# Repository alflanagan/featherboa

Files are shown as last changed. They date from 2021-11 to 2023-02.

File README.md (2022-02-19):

# featherboa

Programmming a [FeatherS2 board](https://feathers2.io/) (ESP32-S2 chip) in Python. The actual implementation is the [CircuitPython port](https://circuitpython.org/board/unexpectedmaker_feathers2/) for the FeatherS2 board.

## What's with the name?

Feather is the name of the controller board I'm using for my robot, and a boa constrictor is, well, cousin to a python at least. (Hey, you try finding an original name on github).

## The Robot

The chip is being used to drive two Adafruit Feather [motor controllers](https://www.adafruit.com/product/2928). Each can drive 8 servos, but the robot uses 12, so they're divided into 6 servos/2 legs per board.

The robot body is based on a [Thingiverse Item](https://www.thingiverse.com/thing:50125)\*. I've included the OpenScad files in this repository, some of them have been re-written by me.

## Project Log

I am (trying to) maintain a [log](./docs/project_log.md) of the progress of this project. Hopefully if you're interested in this
project you can learn from my mistakes along the way.

---

\* Those files are covered by the Creative Commons license [CC BY-SA 3.0](https://creativecommons.org/licenses/by-sa/3.0/).

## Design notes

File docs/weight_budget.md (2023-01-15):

# Featherboa: Weight

## What is a Weight Budget?

For any mobile device, weight is an issue, for two main reasons. First, for a given set of wheels, tractors, or in our case legs, there's a maximum weight the chassis can support and still be able to move. Second, when moving, the more weight moved, the more energy it takes (see document [Energy Budget](energy_budget.md)). So the goal is to minimize the weight.

So a weight budget is the weight of all the pieces and parts, constrained by the amount the robot can reasonably carry.

Since our batteries are the second-largest source of extra weight, the weight budget puts limits on the energy budget, and vice-versa.

## Total Weight

                                |          | Weight|Per Unit |       |                                   |
Part                            | Quantity | Rated | Actual  | Total | Notes                             |
--------------------------------|----------|-------|---------|-------|-----------------------------------|
SG92R Servo Motor               |  12      | 9     | 11.65   | 139.8 | includes cable, mounting screws   |
1200 mAh LiPo battery           |  1       | 23    | 23      | 23    |                                   |
AA Battery, Duracell Alkaline   |  4       | 24    | 24.5    | 98    |                                   |
Leg mount (original)            |  2       |       | 2.5     | 5     |                                   |
Leg mount (wider)               |  2       |       | 4       | 8     |                                   |
Hip                             |  4       |       | 6.9     | 27.6  | includes horns, hot glue          |
4AA Battery Holder              |  1       |       | 11.3    | 11.3  |                                   |
Feather PCA9685 PWM controller  |  2       | 3.9   | 10.2    | 20.4  | Includes headers, 100uF capacitor |
FeatherS2 Microcontroller board |  1       |       | 6.2     | 6.2   | includes headers                  |
Upper Leg                       |  4       |       | 1.8     | 7.2   | includes motor horns, hot glue    |
Body (central bar)              |  1       |       | 0       | 0     |                                   |
Tibia (lower leg)               |  4       |       | 1.7     | 6.8   |                                   |

## Weight Limits

How much can the robot weigh? That's tricky. To stand, the robot needs to weigh less than the strength of the motors that hold the joints in a standing pose.

But we don't want our robot to just stand there, we want it to move. And that means at least one foot will be out of contact with the ground, so the remaining 3 legs have to be capable of bearing the weight.

One can get an estimate of the strength of the legs from the torque specifications of the motors, and the geometry of the parts (specifically the "ulna" and "tibia"). Or, one can directly measure the force required to cause the pose to break down and the leg to start moving.

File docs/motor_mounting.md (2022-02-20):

# Notes on Mounting SG92R MicroServo Motors

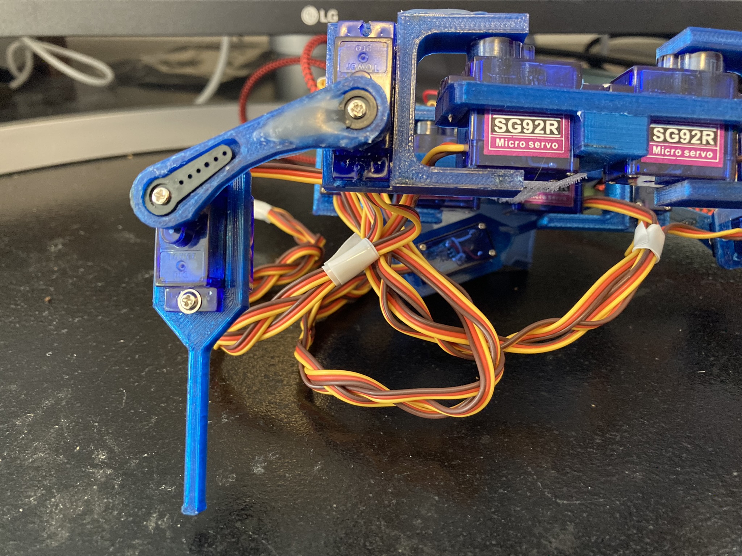
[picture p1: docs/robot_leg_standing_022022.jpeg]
robot leg with three motors


_One of four legs of the robot, more or less in a standing position. From the left, parts are a tibia, an ulna, and a hip. Farthest right is the hip of another leg._

## Overview

There are two basic points of connection between each motor and the body frame. The first is a rectangular hole that exactly fits the main body under the mounting lip. The second is the single point of contact with the gear which actually creates the motion.

This means there are four possible ways to mount each motor (although, as we'll see, some of them are equivalent for some parts.)

motor upright gear on left  motor upright gear on right

motor upside down gear on right
motor upside down gear on left

So the main motor can be on either side of the rectangular hole, and the gear is offset and can be on one side or other.

## The Joints

### Joint: Hip to Body

For the hip joint, the gear has to be on the outside or the joint won't fit. On the other hand, whether you mount the motor right side up or upside down doesn't matter (in terms of the hip motion), because the hip joint is symmetrical.

The only thing to keep in mind is that all the motors should be oriented one way or the other, to keep the sides balanced. Honestly, I'm not sure how much difference even that rule makes, as I haven't tried mixing them up.

### Joint: Hip to Ulna (Upper Leg)

In contrast, all four arrangments matter for this joint. The gear can be towards the top of the body, or towards the bottom; this affects the height (and possibly stability) of the robot. For now at least, I've chosen to mount them gear-down, for greater height. We'll see how it works.

Similarly, the gear can be pointing inside (towards the other leg), or outside away from the body. I've mounted the gears pointing toward the outside, to widen the stance, and reduce interference between front and rear legs on each side.

A further wrinkle: how you mount the motors will affect the code to drive the leg -- namely, does increasing the angle move the rest of the leg up, or down? Our code will have to reverse the rotation for some motors.

### Joint: Ulna to Tibia (Upper Leg to Lower)

The final joint is the lower leg, and the most important constraint is that the leg has to point down (duh). The tibia is symmetrical in the direction of the motor, so the only decision you have to make is whether the gear is on the upper side, or lower toward the "foot". I haven't found a good argument for mounting it lower. Other than that, how it attaches is already determined by how you've mounted the second motor.

## Range of Motion

Each motor has a range of motion, where the gear stops turning at a certain angle each way. You adjust the range of motion of the body part by mounting the horn on the gear at a certain angle.

I tried to set up each motor so that the range of motion of the gear matches the expected motion of the joint. Essentially I'd mount the horn on the gear and manually move the motor back and forth to the stopping points. To adjust the motion, I'd pop the horn off the gear and turn it one way or another, then press it down on the gear again. You may need tweezers or some sort of tool to help get the horn back off the gear.

## Attachment to Gear

The motors each come with two screws, and the body parts have corresponding mouting holes. There really isn't much to say about that other than the orientation as discussed above.

The attachment to the gear -- well, that's a different story. Notice that each gear attachment point has a hole for the gear, and a long shallow vaguely triangular depression in the body. The motors come with several "horns"\* which fit over the gear and extend to one side, or several, to allow connections with various parts. In particular, one horn fits over the gear and extends a triangular part in one direction -- which fits nicely into the depression in the body part.

So, all you have to do is fit the gear through the part with the depression facing up. Then we screw the horn on with the provided small screw, and the horn settles into the depression. When the gear turns, the horn efficiently transfers the force to the given part of the leg.

That's the theory. In reality, when I did that, I discovered a couple of problems. First, the part of the horn that fits over the gear is a bit longer than the hole in the part. Second, the depression is just a bit larger than the actual horn. I expect this is the inevitable result of getting your motors from different manufactures with slightly different specs.

The practical effect of that is that the connection between the motor gear and the leg part is loose, and the part is free to move both up and down the shaft, and back and forth rotationally. This makes for a very loose jointed robot, to the point that the leg becomes very unstable and the whole thing is in constant danger of falling apart.

One solution might be to redo all the parts with the thickness of the hole, and the size of the depression, adjusted to exactly fit the horns you have. I suspect that this will work, at least if the horn is of high enough quality. I haven't tried it as it means resizing a bunch of parts precisely, then re-printing them.

My first thought was: these parts are thermoplastic. If I warm the area to the point where the plastic is malleable, I might be able to reshape it to fit precisely to the horn. I don't know if you can actually do that. When I tried it, I discovered something important about the horns that came with my motors. Namely, the melting point of the plastic is lower than the melting point of the PLA thermoplastic used to print the body parts.

Scratch one body part, and one horm. Fortunately I ordered more motors than the 12 required for the robot, so I had extra. I highly recommend doing that, unless you're one of those people who gets things right on the first try. I have no idea what that would be like.

What I ended up using was a hot glue gun -- I stress again that this a prototype and doesn't have to be pretty. I was able (sometimes) to get the hot glue to fill the depression and stick to the body and the horn. I did not keep track of the number of times I had to retry it for some joints. If you've got a better solution, I'd _love_ to hear about it.

\* I have no idea why they're called that.

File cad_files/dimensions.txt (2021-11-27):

inner diameter center hole: 4.78mm
width of featherwing: 22.9mm
length of featherwing (w/o headers): 50.8mm
height of board + headers: 10.1mm
right-angle header width: 10mm

width lipo battery: 35mm
length lipo: 60mm
height lipo: 5.1mm

width of 4xAA holder: 30mm
height of holder: 32mm
length of holder: 58.6 mm

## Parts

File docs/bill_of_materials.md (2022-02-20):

| Quantity | Description | Supplier | Price EA | Total  |
| --- | --- | --- | --- | --- |
| ?? gms | Thermoplastic Resin for 3D Printer | | | |
| 2 | 8-Channel PWM or Servo FeatherWing Add-on For All Feather Boards | Adafruit | 9.95 | 19.90  |
| 1 | 3x4 Right Angle Male Header Adafruit (4-pack) | Adafruit | 2.95 | 2.95 |
| 1 | FeatherS2 - ESP32-S2 Feather Development Board | Adafruit | 24.95 | 24.95  |
| 1 | Adafruit Micro-Lipo Charger for LiPo/LiIon Batt w/MicroUSB Jack - v1 | Adafruit | 6.95 | 6.95 |
| 1 | Lithium Ion Polymer Battery - 3.7v 1200mAh | Adafruit | 9.95 | 9.95 |
| 12 | Micro servo Tower Pro SG92R | Adafruit | 5.95 | 71.40  |
| 1 | Battery holder: 4 x AAA | found item | | |
| 2 | 100uF 50V capacitor | found item | | |
| | Total Cost | | | 136.10 |

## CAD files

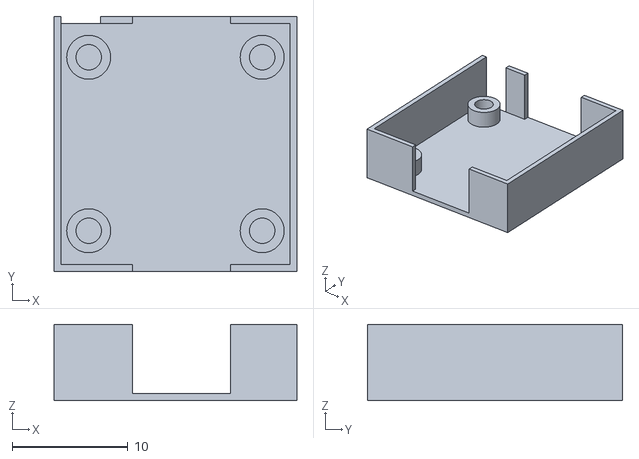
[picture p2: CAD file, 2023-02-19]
cad_files/power_boost.stl
21.0 x 22.1 x 6.60

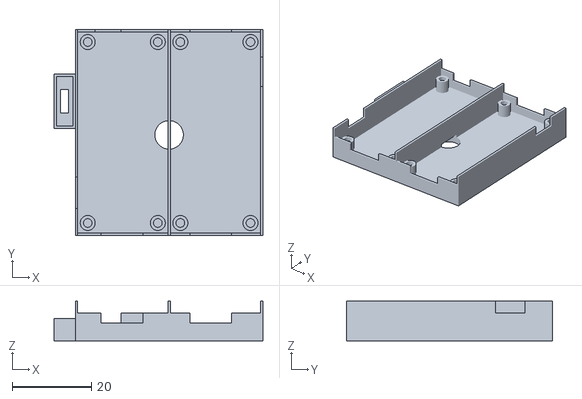
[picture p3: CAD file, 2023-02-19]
cad_files/board_tray2.stl
52.8 x 52.0 x 10.0

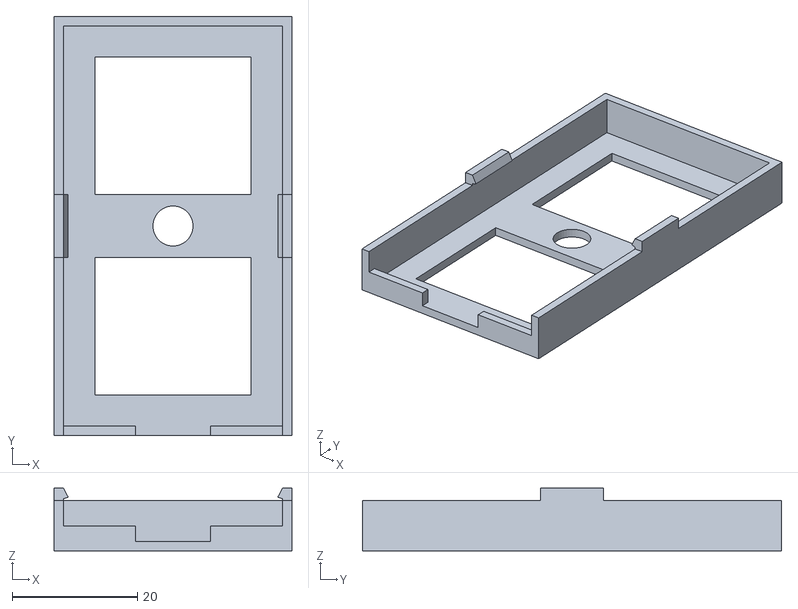
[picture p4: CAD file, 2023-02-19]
cad_files/battery_box.stl
38.0 x 67.0 x 10.0

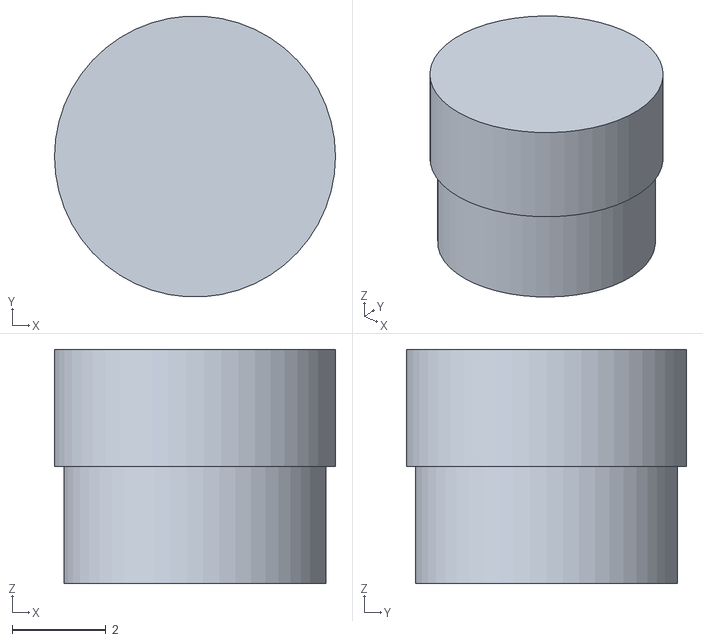
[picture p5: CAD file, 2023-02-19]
cad_files/center_post.stl
6.00 x 5.99 x 5.00

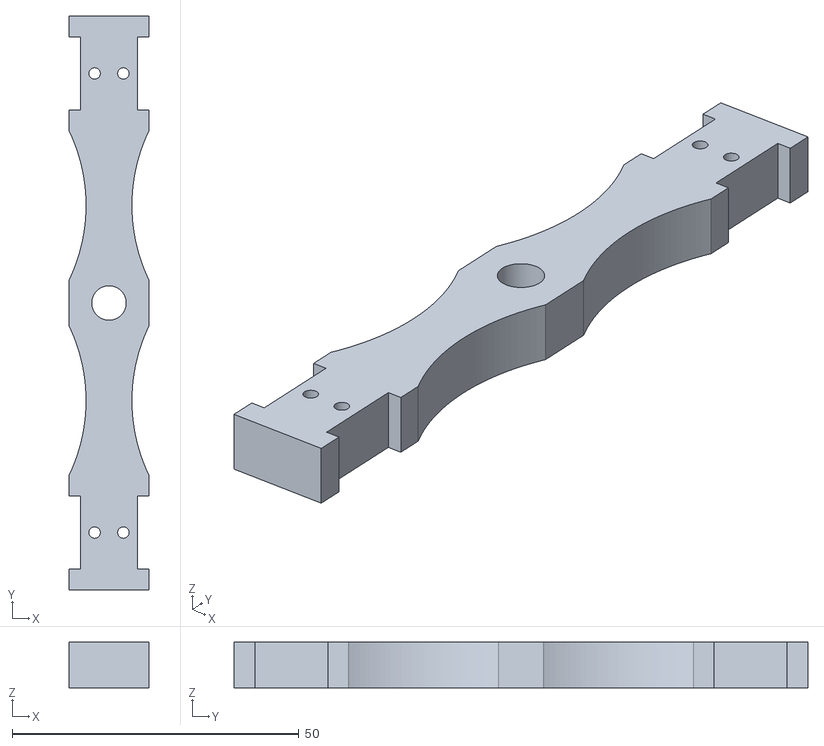
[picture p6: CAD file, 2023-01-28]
cad_files/backbone.stl
14.0 x 100.0 x 8.00

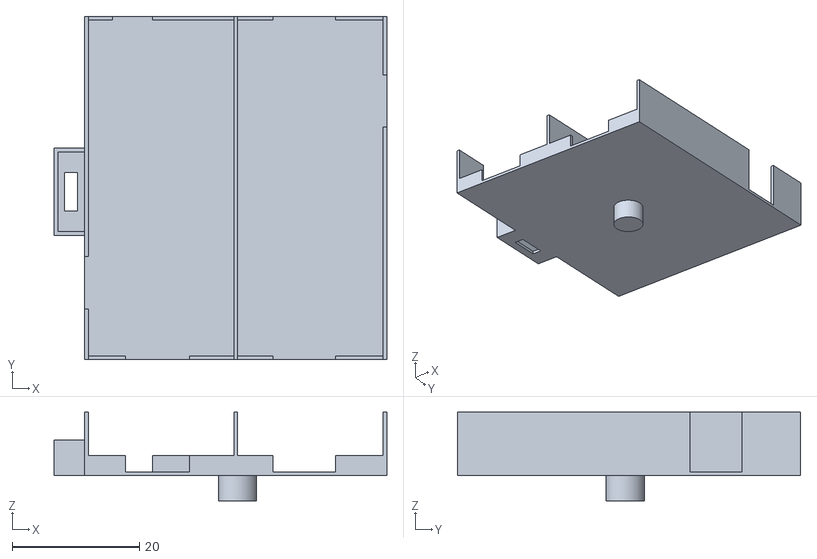
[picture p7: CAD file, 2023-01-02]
cad_files/board_tray.stl
52.4 x 54.0 x 14.0

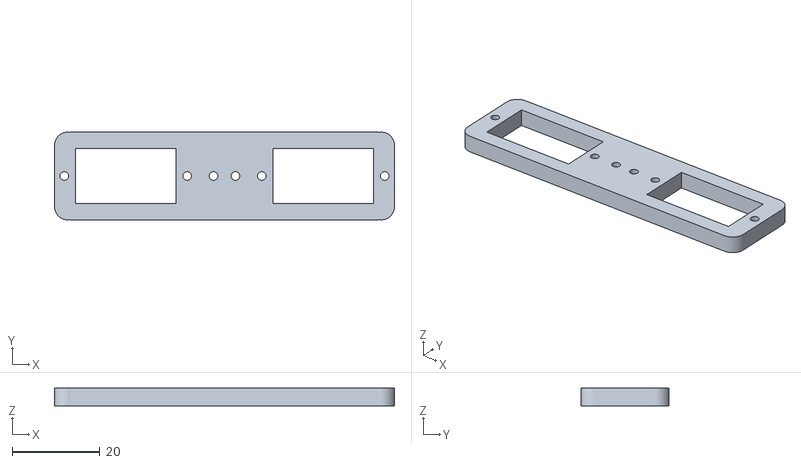
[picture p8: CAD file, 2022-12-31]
cad_files/hip2.stl
77.5 x 20.0 x 4.00

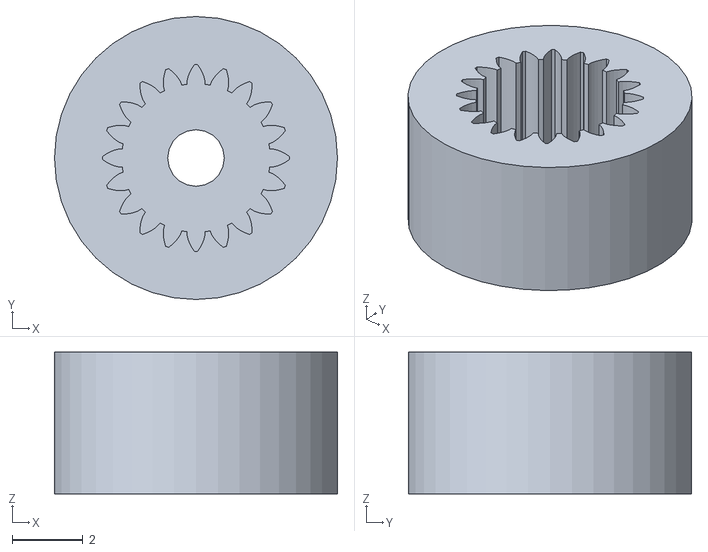
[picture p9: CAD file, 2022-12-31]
cad_files/sg92r_gear.stl
8.00 x 8.00 x 4.00

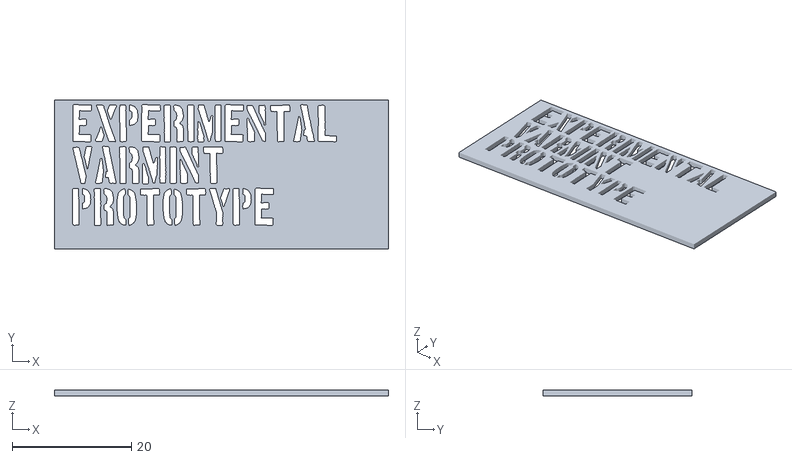
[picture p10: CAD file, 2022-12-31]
cad_files/signage.stl
56.0 x 25.0 x 1.00

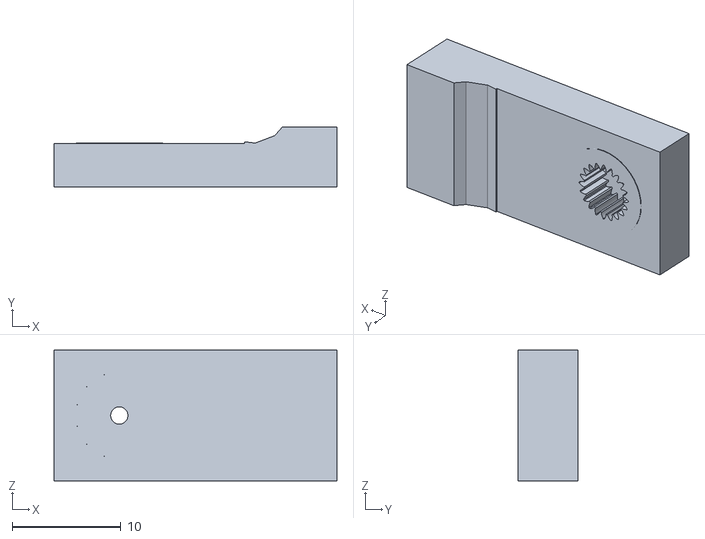
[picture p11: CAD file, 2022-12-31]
cad_files/coxa2.stl
26.0 x 5.50 x 12.0

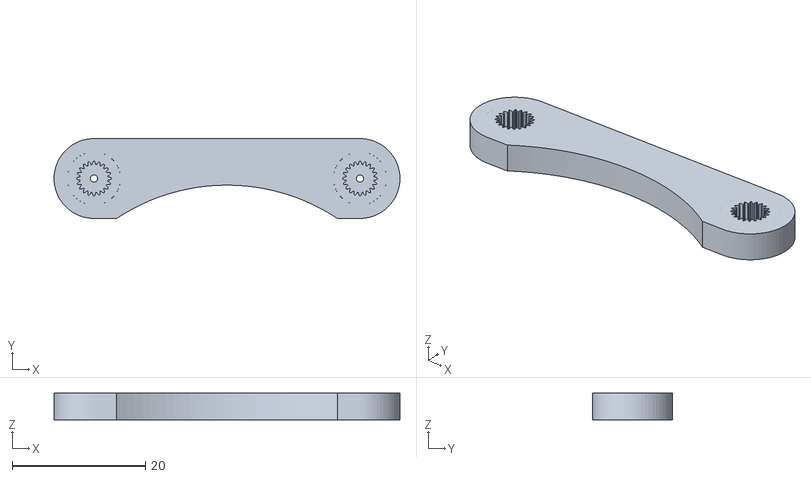
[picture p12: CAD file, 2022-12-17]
cad_files/femur.stl
52.0 x 12.0 x 4.00

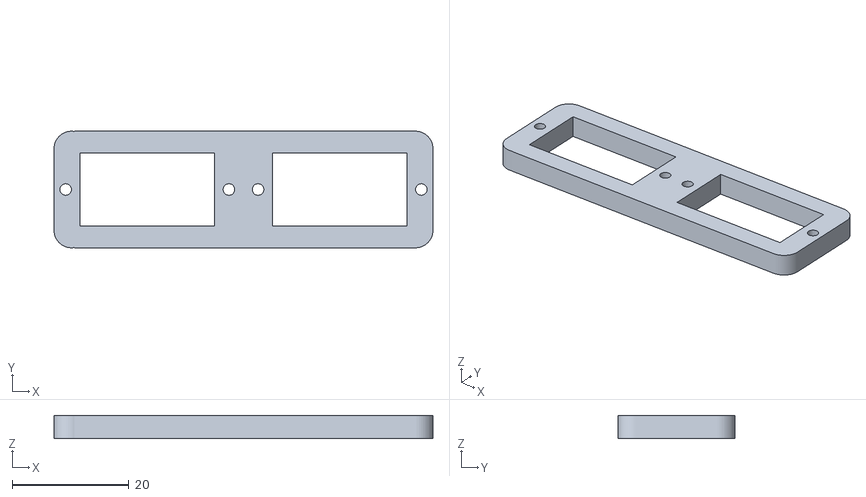
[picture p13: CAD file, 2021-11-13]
cad_files/hip.stl
65.0 x 20.0 x 4.00

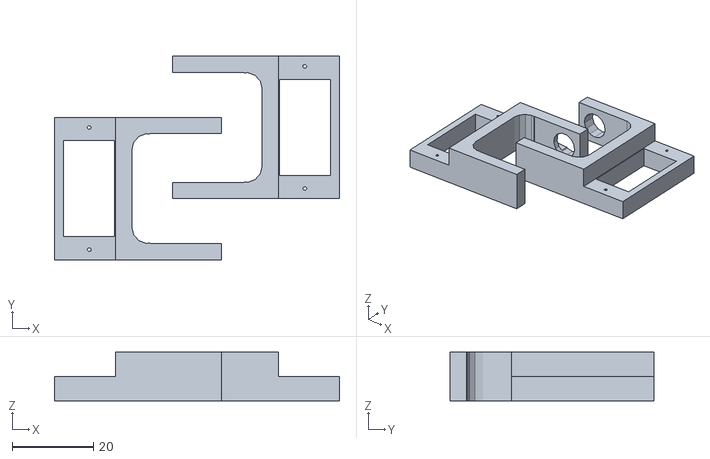
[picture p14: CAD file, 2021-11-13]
cad_files/coxa.stl
70.0 x 50.0 x 12.0

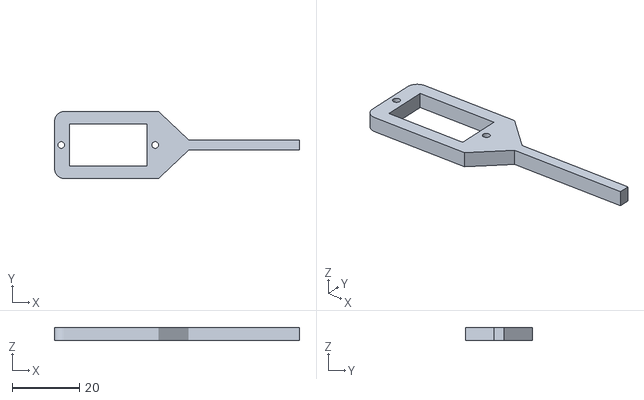
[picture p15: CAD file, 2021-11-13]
cad_files/tibia.stl
73.0 x 20.0 x 4.00

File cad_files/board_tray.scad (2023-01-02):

// tray for attaching feather boards to body assembly
// 1 unit = 1 mm

/* [Utility] */
// overlap to indicate joined objects
overlap = 0.01;

/* [Center Post] */
// center mounting hole in the backbone
center_hole_radius = 3;
// height of robot "backbone"
backbone_height = 8;

/* [Servo Board] */
// servo board w/power and right-angle headers
featherwing_width = 22.9;
// length of servo controller board
featherwing_length = 52.8;
// height of board + power post
featherwing_height = 10;

// mc board w/ through-hole leads
circuit_board_thickness = 2.6;

/* [Thickness] */
// sidewall width (also for end lips)
sidewall_width = 0.6;
// bottom thickness -- biggest effect on mass
tray_bottom_thickness = 0.6;
// thickness of switch box walls
switch_box_thickness = 0.6;

/* [Power Post Cutouts] */
// size of cutout for mc board power
power_post_width = 8.2;
// location of power cutout
power_post_from_end = 8;

/* [Power Switch Box] */
// width of power switch (y-dimension)
switch_width = 12.58;
// length of power switch (x-dimension)
switch_length = 4.19;
// height to hold switch but not block
switch_height = 5.6;
switch_wires_length = 2;
switch_wires_width = 6;

/* [End Lip Cutouts ] */
// usb-c connector on featherS2
usb_c_width = 10;
// distance from edge with power post cutout
usb_c_offset = 6.5;
// QWIIC (I2C) connector on featherS2
i2c_width = 6.3;
// distance from edge w/ power post cutout
i2c_offset = 4.42;
// motor controller headers
mc_width = 9.85;
// distance from edge w/ power post cutout
mc_offset = 7.5;

/* General Approach -----------------------------------------------------*/
/*
 * After a lot of experimentation, I've settled on the following best practice.
 * Each part is rendered by a module at 0, 0, 0 without translation (except
 * for overlap) or centering. <del>A separate module calculates the translation to
 * the final location.</del>
 * The final translation is done by the parent module / object.
 */

/* Parts  ---------------------------------------------------------------*/

/*
 * Draws a flat rectangle from 0,0,0, sized to hold two featherwing boards
 * parallel on the longer side. Includes space for sidewalls, etc.
 */
module
tray_bottom()
{
  cube([
    featherwing_width * 2 + sidewall_width * 3,
    featherwing_length + sidewall_width * 2,
    tray_bottom_thickness
  ]);
}

/*
 * Draws a vertical cylinder of a size to extend from the base through
 * the hole in the backbone part.
 */
module
center_post()
{
  cylinder($fn = 64,
           r = center_hole_radius,
           h = backbone_height / 2);
}

/*
 * Draws a flat rectangle the length of a feather board and height
 * of featherwing_height. Seperates and stabilizes the board position.
 */
module
sidewall()
{
  cube([
    sidewall_width + overlap,
    featherwing_length + 2 * sidewall_width,
    featherwing_height
  ]);
}


/*
 * Cutout in end_lip to allow access for USB-C connector or motor controller
 * headers (which are roughly the same width)
 */
module
usb_notch() {
  cube([
    usb_c_width, 
    sidewall_width + overlap * 2,
    featherwing_height
  ]);
}

/*
 * Cutout in end_lip to allow access for QWIIC connector.
 */
module
qwiic_notch() {
  cube([
    i2c_width, 
    sidewall_width + overlap * 2,
    featherwing_height
  ]);
}

/*
 * Cutout in sidewall to provide access to power supplies (battery connector for
 * micro, 5 volts for motor controllers).
 */
module
power_notch()
{
  translate([-overlap, -overlap, -overlap])
    cube([
      sidewall_width + overlap * 3, // 2 just not enough, somehow
      power_post_width,
      featherwing_height + overlap * 2
    ]);
}

/*
 * Cutout in end_lip to fit horizontal headers.
 */
module
mc_header_notch() {
  cube([
    mc_width, 
    sidewall_width + overlap * 2,
    featherwing_height
  ]);
}


/*
 * A low wall that spans the two board trays.
 */
module
end_lip()
{
  cube(
    [
      featherwing_width * 2 + sidewall_width * 3,
      sidewall_width,
      tray_bottom_thickness + circuit_board_thickness
    ]
  );
}

/*
 * A small box to contain a switch I happened to have on hand.
 * You'll need to at least set switch_length and switch_width to match
 * your switch, and possibly modify the cutout for the leads.
 */
module
switch_holder()
{
  difference()
  {
    union()
    {
      cube([ switch_length, switch_width, switch_box_thickness ]);
      translate([ 0, -switch_box_thickness + overlap, 0 ])
        cube([ switch_length, switch_box_thickness, switch_height ]);
      translate([ 0, switch_width - overlap, 0 ])
        cube([ switch_length, switch_box_thickness, switch_height ]);
      translate([ -switch_box_thickness + overlap, -switch_box_thickness, 0 ])
        cube([
               switch_box_thickness,
               switch_width + switch_box_thickness * 2,
               switch_height
        ]);
      translate([ switch_length - overlap, -switch_box_thickness, 0 ])
        cube([
          switch_box_thickness,
          switch_width + switch_box_thickness * 2,
          switch_height
        ]);
    } // union
    translate([
      (switch_length - switch_wires_length) / 2,
      (switch_width - switch_wires_width) / 2,
      -switch_box_thickness / 2
    ])
      cube([
        switch_wires_length,
        switch_wires_width,
        switch_box_thickness * 2
      ]);
  }; // difference
}



/* Assembly ---------------------------------------------------------------*/

module
board_tray()
{
  difference()
  {
    union()
    {
      tray_bottom();
      sidewall();
      translate([featherwing_width + sidewall_width, 0, 0])
        sidewall();
      translate([(featherwing_width + sidewall_width) * 2, 0, 0])
        sidewall();
      end_lip();
      translate([0, featherwing_length + sidewall_width, 0])
        end_lip();
      translate([-switch_length, (featherwing_length - switch_width) / 2, 0])
        switch_holder();
      translate([
        featherwing_width + 2 * sidewall_width,
        featherwing_length / 2,
        -backbone_height / 2 + overlap
      ])
        center_post();
    }  // union
    translate([0, power_post_from_end, tray_bottom_thickness])
      power_notch();
    translate([
      featherwing_width * 2 + sidewall_width * 2,
      featherwing_length - power_post_width - power_post_from_end,
      tray_bottom_thickness
    ])
      power_notch();
    translate([usb_c_offset, -overlap, tray_bottom_thickness])
      usb_notch();
    translate([
      i2c_offset, 
      featherwing_length + sidewall_width - overlap,
      tray_bottom_thickness
    ])
      qwiic_notch();
    translate([
      (featherwing_width + sidewall_width) * 2 - mc_width - mc_offset,
      -overlap,
      tray_bottom_thickness
    ])
      mc_header_notch();
    translate([
      (featherwing_width + sidewall_width) * 2 - mc_width - mc_offset,
      featherwing_length + sidewall_width - overlap,
      tray_bottom_thickness
    ])
      mc_header_notch();
  } // difference
}

board_tray();

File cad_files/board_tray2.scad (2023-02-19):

include <screw_holders.scad>;

// tray for attaching feather boards to body assembly
// 1 unit = 1 mm

/* [Utility] */
// overlap to indicate joined objects
overlap = 0.01;

/* [Center Post] */
// center mounting hole in the backbone
// upper part is a bit wider -- see center_post.scad
// center_hole_radius = 3.15; // 2.84 in real life, 4 => 3.76
center_hole_radius = 3.7;
// height of robot "backbone"
backbone_height = 8;

/* [Servo Board] */
//https://learn.adafruit.com/adafruit-feather/feather-specification?view=all#feather-and-wing-sizes-2861831
// servo board w/power and right-angle headers
featherwing_width = 22.8;
// length of servo controller board
featherwing_length = 50.8;
// height of board + power post
featherwing_height = 10;
hole_to_hole_narrow = 17.7;
hole_to_hole_wide = 45.7;

// mc board (includes screw holes)
circuit_board_thickness = 5;

/* [Thickness] */
// sidewall width
sidewall_width = 0.6;
// bottom thickness -- biggest effect on mass
tray_bottom_thickness = 2;
// tray_bottom_thickness = 0.8;

// z-offset of center post and matching hole
center_post_offset = -backbone_height / 2 - tray_bottom_thickness - overlap;

/* [Power Switch Box] */
// width of power switch
switch_width = 12.58;
// length of power switch
switch_length = 4.19;
// height to hold switch but not block
switch_height = 5.6;
switch_wires_length = 2;
switch_wires_width = 6;
// thickness of switch box walls
switch_box_thickness = 0.6;

/* [Board i2c Connector] */
// distance from edge
board_i2c_to_edge = 5;
// width of connector
board_i2c_width = 6.55;

/* [Board Power Connector] */
board_pwr_width = 8.0;
board_pwr_to_edge = 6.8;

/* [USB Connector] */
// actual connector not this wide, but board tab is
// distance from edge to start of tab
usb_to_edge = 6.5;
// width of tab
usb_width = 10.65;

/* [Motor Controller] */
// size of cutout for mc board power
power_post_width = 7.5;
// location of power cutout
power_post_from_end = 5.7;
// motor connections
side_header_width = 10.5;
side_header_offset = 6.1;


/* General Approach -----------------------------------------------------*/
/*
 * After a lot of experimentation, I've settled on the following best practice.
 * Each part is rendered by a module at 0, 0, 0 without translation (except
 * for overlap) or centering. A separate module calculates the translation to 
 * the final location.
 */
 
/* Parts  ---------------------------------------------------------------*/

/*
 * Draws a flat rectangle from 0,0,0, sized to hold two featherwing boards
 * parallel on the longer side. Includes space for sidewalls, etc.
 */
module
tray_bottom()
{
    cube(
        [
            featherwing_width * 2 + sidewall_width * 3,
            featherwing_length + sidewall_width * 2,
            tray_bottom_thickness
        ]
    );
}

/*
 * Draws a vertical cylinder of a size to extend from the base through
 * the hole in the backbone part.
 */
module
center_post()
{
    cylinder($fn = 50,
             r = center_hole_radius,
             h = tray_bottom_thickness + backbone_height / 2);
}


/*
 * Draws a flat rectangle the length of a feather board and height
 * of featherwing_height. Seperates and stabilizes the board position.
 */
module
sidewall()
{
    cube([ 
        sidewall_width + overlap, 
        featherwing_length + 2 * sidewall_width,
        featherwing_height 
    ]);
}

module
power_notch()
{
    cube([
            sidewall_width + 1,
            power_post_width,
            featherwing_height
        ]);
}

module
end_lip(xmul)
{
        cube([
                xmul * (featherwing_width * 2 + sidewall_width * 3),
                sidewall_width,
                tray_bottom_thickness +
                circuit_board_thickness
            ]);
}

module
switch_holder()
{
    difference()
    {
        union()
        {
            cube([ switch_length, switch_width, switch_box_thickness ]);
            translate([ 0, -switch_box_thickness + overlap, 0 ])
                cube([ switch_length, switch_box_thickness, switch_height ]);
            translate([ 0, switch_width - overlap, 0 ])
                cube([ switch_length, switch_box_thickness, switch_height ]);
            translate(
                [ -switch_box_thickness + overlap, -switch_box_thickness, 0 ])
                cube([
                    switch_box_thickness,
                    switch_width + switch_box_thickness * 2,
                    switch_height
                ]);
            translate([ switch_length - overlap, -switch_box_thickness, 0 ])
                cube([
                    switch_box_thickness,
                    switch_width + switch_box_thickness * 2,
                    switch_height
                ]);
        }
        translate([
            (switch_length - switch_wires_length) / 2,
            (switch_width - switch_wires_width) / 2,
            -switch_box_thickness / 2
        ])
            cube([
                switch_wires_length,
                switch_wires_width,
                switch_box_thickness * 2
            ]);
    };
}

module
board_i2c()
{
    cube([board_i2c_width, sidewall_width + 2 * overlap, featherwing_height]);
}

module
usb_connector()
{
    cube([usb_width, sidewall_width + 2 * overlap, featherwing_height]);
}

module
motor_connections()
{
    cube([side_header_width, sidewall_width + 2 * overlap, featherwing_height]);
}

module
board_power()
{
    cube([sidewall_width + 1,
          board_pwr_width,
          featherwing_height]);
}

/* Assembly ---------------------------------------------------------------*/

module
board_tray()
{
    difference()
    {
        union()
        {
            tray_bottom();
            sidewall();
            translate([featherwing_width + sidewall_width, 0, 0])
                sidewall();
            translate([(featherwing_width + sidewall_width) * 2, 0, 0])
                sidewall();
            end_lip(1);
            translate([0, featherwing_length + sidewall_width, 0])
                end_lip(1);
            translate([-switch_length - sidewall_width + overlap, 
                       featherwing_length * 2 / 3 - switch_width / 2,
                       0])
                switch_holder();
            translate([featherwing_width + sidewall_width, sidewall_width, 0])
              rotate([0, 0, 90])
                four_holes(tray_bottom_thickness);
            translate([(featherwing_width + sidewall_width) * 2,
                        sidewall_width,
                        0])
              rotate([0, 0, 90])
                four_holes(tray_bottom_thickness);
        }
                translate([(featherwing_width * 2 + sidewall_width * 3) / 2,
                            featherwing_length / 2,
                            center_post_offset / 2])
                    center_post();
        translate([board_i2c_to_edge, 
                   featherwing_length + sidewall_width - overlap,
                   tray_bottom_thickness + circuit_board_thickness / 2])
            board_i2c();
        translate([usb_to_edge,
                   -overlap,
                   tray_bottom_thickness + circuit_board_thickness / 2])
            usb_connector();
        translate([featherwing_width * 2 - side_header_width - side_header_offset,
                   featherwing_length + sidewall_width - overlap,
                   tray_bottom_thickness + circuit_board_thickness / 2])
            motor_connections();
        translate([featherwing_width * 2 - side_header_width - side_header_offset, 
                   -overlap, 
                   tray_bottom_thickness + circuit_board_thickness / 2])
            motor_connections();
        translate([-overlap, board_pwr_to_edge, tray_bottom_thickness + circuit_board_thickness])
            board_power();
        translate([featherwing_width * 2 + sidewall_width * 2 - 0.5,
                   featherwing_length - power_post_width - power_post_from_end,
                   tray_bottom_thickness + circuit_board_thickness])
            power_notch();
    }
}

board_tray();

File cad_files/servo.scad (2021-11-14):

// 3dof quad
//
// servo

module
servo(a = 30,
      b = 23,
      c = 27,
      d = 12,
      e = 33,
      f = 16,
      flange_thickness = 2,
      top_cap_pct = 0.5)
{
    rem_height = c - flange_thickness - f;
    top_cap_height = rem_height * top_cap_pct;
    roundel_height = rem_height * (1.0 - top_cap_pct);

    translate([ 0, -d / 2, 0 ]) union()
    {
        translate([ 0, 0, flange_thickness / 2 ])
            cube([ d, e, flange_thickness ], center = true);
        translate([ 0, 0, -f / 2 ]) cube([ d, b, f ], center = true);
        translate([ 0, 0, flange_thickness + top_cap_height / 2 ])
            cube([ d, b, top_cap_height ], center = true);
        translate(
            [ 0, b / 2 - d / 2, flange_thickness + top_cap_height ]) union()
        {
            cylinder(r = d / 2, h = roundel_height);
            translate([ 0, 0, roundel_height ]) cylinder(r = 3, h = 3);
        }
    }
}

color("blue") servo();

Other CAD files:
cad_files/screw_holders.stl
cad_files/servo_arm.scad
cad_files/assembly.scad
cad_files/backbone.scad
cad_files/battery_box.scad
cad_files/center_post.scad
cad_files/coxa.scad
cad_files/coxa_2.scad
cad_files/coxa_2.stl
cad_files/femur.scad
cad_files/header_rows.scad
cad_files/hip.scad
cad_files/hip_dimensions.scad
cad_files/power_boost.scad
cad_files/screw_holders.scad
cad_files/sg92r_gear.scad
cad_files/signage.scad
cad_files/tibia.scad

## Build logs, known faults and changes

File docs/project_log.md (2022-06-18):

## 11/27/21

1. The servo mounts on the hip piece of robot touch each other. I want some space between them for the right-angle
   headers on the motor controller featherwing. So, I rewrote hip.scad to base it on a few distance variables, and added
   a center space between the servo mounts.
2. On the other hand, it might be easier/better to mount the motor controllers underneath the body piece, which would
   make that unnecessary. However, problem with that is, where will the battery go?
3. I can stack the motor controllers with headers and fit them over the center body, but where will the feathers2 go?
   Not sure that I want to stack all 3, for one thing it makes it harder to get to the controller boards if necessary.
4. Also: need to find electrolytic capacitors at the space and add to controller boards. I _think_ I settled on about
   100 uF for the capacitance, we'll see how that works.

Later, at the space:

1. added 100 uF caps to the motor controller boards. Discovered that installing them upright interfered with stacking
   headers, so removed them and installed some laying sideways.
2. Printed a hip piece with a wider stance. Noticed I didn't have holes to match the mount holes in the backbone piece.
   I can always drill some.
3. Spent a fair amount of time attempting to make a row of holes in a printed piece which match the pins in a standard
   header. Surprisingly hard to get a match. Should use standard measurements but I'm not convinced printer is
   calibrated properly.
4. Clipped male leads on stacking header at bottom of motor controller stack, as I didn't want to put them on top of
   main board anyway.
5. Installed male headers into second motor controller, stacked on top of the first. Seems to be the most efficient use
   of space possible.
6. Need to add holder for on-off switch I found for the motor power supply, which should be manually switchable.

12/4/21

1. added (back) holes in hip.scad that mount to the backbone piece
2. switch dimensions: 11.58 mm x 4.19 mm x 5.6 mm (height). wires project from the bottom have a width of 6 mm x 2 mm (
   width depends on how wires are bent. need to add shrinkwrap tubing)

2/19/22

Some catchup:

   1. Have a holder printed with a switch, which is connected to a 4-AA battery holder and the Vin of one of the motor controller
      boards. Boards are held in place with velcro (hey, it's a prototype.) One motor controller is stacked on top of the
      FeatherS2 board.
   2. Circuitpython is now at 7.2.0-alpha2, for better feathers2 support. Alpha 1 had some real problems, but alpha 2 seems to
      have resolved them and is working nicely. A release candidate version is out now, I will probably upgrade again soon.
   3. Somewhere in here I recommend a VS Code extension for circuitpython at https://github.com/joedevivo/vscode-circuitpython.
      Unfortunately I've run into too many unresolved issues and had to remove it. It apparently is not being maintained since
      mid-2021. (The usual sad fate of many open-source projects.) In fact, I've forked it, but as my knowledge of Typescript is
      rudimentary, and my knowledge of VS Code extensions basically non-existent, don't hold your breath for fixes soon.
   4. Pretty sure the 4-AA battery design is just too heavy, I need to go with AAAs or probably a couple of li-poly batteries.

TODOS:

   1. Further updates to board holder. The side notches are still a little bit off, and I should add notches for the connectors on the board ends. However, the velcro is (for now) lifting the connectors higher than the end walls anyway. Ideally you'd be able to snap the boards into the holder and have notches for everything, lined up properly.
   2. A lot of coding. I'm still not happy with the data structures for representing motors, motor controllers, and the four legs, to say nothing of actually programming coherent movement.

Done:

   1. Hooked up motors for left side and spent some time matching servo motor # on the board to position on the robot. Note that angles are very inconsistent, need to calibrate.
   2. A lot of code cleanup and refactoring.

3/2/2022

   1. Printed new version of board holder. Immediately saw that third tray for ESP32-S2 board would block connectors on the motor controller boards. Note: try to avoid permanent headers until you've decided on positions for all the electronic components.

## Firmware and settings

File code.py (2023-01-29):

import gc
import os
import sys
import time
from random import randrange

import board
import digitalio
import espidf
import wifi

from constants import NS_PER_SECOND
from lib.feathers2 import enable_LDO2, led_set
from lib.legs import Motor, Servo, motor_angle_calibration
from lib.networking import connect_home_network

# built-in adafruit modules for feathers2
# _bleio, adafruit_bus_device, adafruit_pixelbuf, aesio, alarm, analogio, atexit, audiobusio,
# audiocore, audiomixer, binascii, bitbangio, bitmaptools, board, busio, canio, countio, digitalio,
# displayio, dualbank, errno, fontio, framebufferio, frequencyio, getpass, i2cperipheral,
# imagecapture, ipaddress, json, keypad, math, microcontroller, msgpack, neopixel_write, nvm,
# onewireio, os, paralleldisplay, ps2io, pulseio, pwmio, qrio, rainbowio, random, re, rgbmatrix,
# rotaryio, rtc, sdcardio, sharpdisplay, socketpool, ssl, storage, struct, supervisor, synthio,
# terminalio, time, touchio, traceback, ulab, usb_cdc, usb_hid, usb_midi, vectorio, watchdog, wifi

# dir(board):
# 'A0', 'A1', 'A10', 'A2', 'A3', 'A4', 'A5', 'A6', 'A7', 'A8', 'A9', 'AMB', 'APA102_MOSI',
# 'APA102_SCK', 'D0', 'D1', 'D10', 'D11', 'D12', 'D13', 'D14', 'D15', 'D16', 'D17', 'D18',
# 'D19', 'D20', 'D21', 'D23', 'D24', 'D25', 'D4', 'D5', 'D6', 'D9', 'DAC1', 'DAC2', 'I2C',
# 'IO0', 'IO1', 'IO10', 'IO11', 'IO12', 'IO14', 'IO17', 'IO18', 'IO21', 'IO3', 'IO33', 'IO35',
# 'IO36', 'IO37', 'IO38', 'IO4', 'IO43', 'IO44', 'IO5', 'IO6', 'IO7', 'IO8', 'IO9', 'LDO2',
# 'LED', 'MISO', 'MOSI', 'RX', 'SCK', 'SCL', 'SDA', 'SPI', 'TX', 'UART', 'board_id'

# dir(feathers2)
# 'DigitalInOut', 'Direction', 'Pull', 'board', 'time', 'led_blink', 'led13', 'led_set'

# feathers2 module sets led13, OUTPUT
# feathers2.led13.direction = digitalio.Direction.OUTPUT

# using IO4 turns off LED function and behaves like ordinary pin
amber_led = digitalio.DigitalInOut(board.AMB)
amber_led.direction = digitalio.Direction.OUTPUT
# .pull is not used when direction = OUTPUT

""" did_setup = False

def setup():
    global did_setup
    if did_setup:
        return
    did_setup = True
    networking.setup()

"""


def say_hello():
    # Say hello
    print("\nHello from FeatherS2!")
    print("---------------------\n")


def show_mem():
    # Show available memory
    print("Memory Info - gc.mem_free()")
    print("---------------------------")
    print("{:,} Bytes\n".format(gc.mem_free()))

    flash = os.statvfs("/")
    flash_size = flash[0] * flash[2]
    flash_free = flash[0] * flash[3]
    # Show flash size
    print("Flash - os.statvfs('/')")
    print("---------------------------")
    print("Size: {:,} Bytes\nFree: {:,} Bytes\n".format(flash_size, flash_free))


def show_network():
    # useful, but takes a few seconds
    print("Networking")
    print("--------------")

    print(
        "AP MAC Address: " + ":".join(["%x" % byt for byt in wifi.radio.mac_address_ap])
    )

    wifi.radio.start_ap("quad_walker")
    connect_home_network()

    print("IP Address " + str(wifi.radio.ipv4_address_ap))
    print("--------------")
    # dns 192.168.1.1


class RandomBlinkLED:
    # looks like each instance is about 87 bytes
    def __init__(self, max_delay):
        self.max_delay = max_delay
        self.mark = time.monotonic_ns()
        self.led_state = False

    def check(self):
        if time.monotonic_ns() > self.mark:
            led_set(self.led_state)
            self.led_state = not self.led_state
            self.mark += int(
                randrange(1_000) / 1_000.0 * self.max_delay * NS_PER_SECOND
            )

    @classmethod
    def run(cls):
        blink_led = cls(2.0)
        print("blinking LED...")
        while True:
            blink_led.check()


def testServos():
    servos = {}
    missing = []
    for i2c_channel in [0x40, 0x41]:
        try:
            servos[i2c_channel] = Servo(address=i2c_channel, channels=8)
        except ValueError:
            missing.append(hex(i2c_channel))

    if missing:
        if len(missing) > 1:
            print(f'Failed to find I2C devices on channels {", ".join(missing)}')
        else:
            print(f"Failed to find an I2C device at channel {missing[0]}")
        sys.exit()

    for num in [
        Motor.LEFT_FRONT_HIP,
        Motor.LEFT_FRONT_UPPER,
        Motor.LEFT_FRONT_LOWER,
        Motor.LEFT_REAR_HIP,
        Motor.LEFT_REAR_UPPER,
        Motor.LEFT_REAR_LOWER,
    ]:
        print("testing motor index " + str(num))
        servos[0].kit.servo[num].angle = motor_angle_calibration[num]
        # sleep(2)


def show_heap():
    print("\nHeap")
    print("--------------")
    print(f"Total PSRAM: {espidf.get_total_psram():,} bytes")
    print(f"Reserved PSRAM: {espidf.get_reserved_psram():,} bytes")
    print(f"Heap size: {espidf.heap_caps_get_total_size():,} bytes")
    print("Heap free: {:,} bytes".format(espidf.heap_caps_get_free_size()))
    print("Mem allocated: {:,} bytes".format(gc.mem_alloc()))
    print("Mem free: {:,} bytes".format(gc.mem_free()))
    print("--------------")


def main():
    # Make sure the 2nd LDO is turned on
    enable_LDO2(True)
    # Turn on the internal blue LED
    led_set(True)
    say_hello()

    # servo0 = Servo(address=0x41, channels=8)

    # fred = esp32.freq()
    # print("CPU")
    # print("---------------------------")
    # print("Frequency {:,}".format(fred))

    uart = board.UART()
    print(f"board connected at {uart.baudrate} baud\n")
    show_mem()
    show_network()
    connect_home_network()
    show_heap()


main()

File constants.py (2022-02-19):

"""
Useful global constants
"""
import board

__all__ = ["PIN_MAP", "NS_PER_SECOND"]

# feathers2 board pin map: (mostly for reference)
# pins in the same row are equivalent
PIN_MAP = [
    [board.A0, board.D14, board.DAC1, board.IO17],
    [board.A1, board.D15, board.DAC2, board.IO18],
    [board.A10, board.D5, board.IO1],
    [board.A2, board.D16, board.IO14],
    [board.A3, board.D17, board.IO12],
    [board.A4, board.D18, board.IO6],
    [board.A5, board.D19, board.IO5],
    [board.A6, board.D13, board.IO11],
    [board.A7, board.D12, board.IO10],
    [board.A8, board.D9, board.IO7],
    [board.A9, board.D6, board.IO3],
    [board.AMB, board.IO4],
    [board.APA102_MOSI],
    [board.APA102_SCK],
    [board.D0, board.IO44, board.RX],
    [board.D1, board.IO43, board.TX],
    [board.D10, board.IO8, board.SDA],
    [board.D11, board.IO9, board.SCL],
    [board.D20, board.IO33],
    [board.D21, board.IO38],
    [board.D23, board.IO37, board.MISO],
    [board.D24, board.IO35, board.MOSI],
    [board.D25, board.IO36, board.SCK],
    [board.D4, board.IO0],
    [board.IO21, board.LDO2],
    [board.LED],
]

NS_PER_SECOND = 1_000_000_000.0

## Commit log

2021-11-13 add CAD files for robot parts
    [assembly.scad, backbone.scad, backbone.stl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]
2021-11-14 formatted w/openscad-format; no functional change
    [assembly.scad, backbone.scad, coxa.scad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]
2021-11-14 add missing variable inits
    [assembly.scad]
2021-11-16 CAD design for tray for feather boards
    [board_tray.scad]
2021-11-27 parameterize hip, add center space
    [hip.scad]
2021-11-28 separate variables into separate file, for reuse
    [hip.scad, hip_dimensions.scad]
2021-11-28 connect to home network, start legs module
2021-12-04 fix length calculation
    [board_tray.scad]
2021-12-04 add holes for screws to backbone
    [hip.scad]
2021-12-04 add box on side for power supply switch
    [board_tray.scad]
2021-12-12 tweak tray length, switch box size
    [board_tray.scad]
2021-12-12 label for robot box
    [signage.scad]
2021-12-12 post to attach tray to backbone
    [center_post.scad]
2021-12-12 ignore stl files (derived), config file
2022-01-22 add __pycache__ in case
2022-02-06 add setup for legs, task for blinking LED
2022-02-19 Add notes to catch up to current status
2022-02-19 document circuitpython library modules used on feathers2
2022-02-19 modules for standard PCB header leads
    [header_rows.scad, test_lead_row.scad]
2022-02-19 set up left leg motors to match wiring
2022-02-19 prelim calibration for left side motors
2022-02-20 Add document describing motor mounts on the robot
2022-02-20 Add BOM
2022-02-21 add third_tray(); tweak power notches
    [board_tray.scad]
2022-06-19 fix hip() call
    [assembly.scad]
2022-06-19 rework for better fit, lower material cost
    [board_tray.scad]
2022-08-14 ignore local bootloader stuff, wing IDE config
2022-08-14 remove unused spi module
2022-12-11 new stencil font for sign
    [signage.scad]
2022-12-11 some tweaks, successful print
    [test_lead_row.scad]
2022-12-17 redone to exactly fit motor gear, without plastic arm
    [femur.scad, femur.stl]
2022-12-18 adapt parts to fit motor gear exactly
    [coxa_2.scad, femur.scad, sg92r_gear.scad]
2022-12-31 A press-fit holder for li-ion battery
    [battery_box.scad]
2022-12-31 remove irrelevant file
    [test_lead_row.scad]
2022-12-31 Add some .stl files for those w/o openscad
    [battery_box.stl, board_tray.stl, coxa2.stl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]
2023-01-01 lower lip for battery insertion, reduce height
    [battery_box.scad, battery_box.stl]
2023-01-01 formatting with openscad-format
    [assembly.scad]
2023-01-01 place center post
    [board_tray.scad]
2023-01-02 move parts into proper position, fix indents, comments
    [board_tray.scad]
2023-01-02 add notches in vertical walls
    [board_tray.scad, board_tray.stl]
2023-01-15 new board tray design, screw hole test
    [board_tray2.scad, screw_holders.scad]
2023-01-15 Size to fit screws I have.
    [screw_holders.scad, screw_holders.stl]
2023-01-16 Add screw holes for 2 boards
    [board_tray2.scad, board_tray2.stl, screw_holders.scad]
2023-01-22 final (??) design for 4 boards and switch
    [board_tray2.scad, board_tray2.stl, screw_holders.scad]
2023-01-28 lengthen, tweak post hole
    [backbone.scad, backbone.stl]
2023-02-19 make wider cylinder less wide
    [center_post.scad, center_post.stl]
2023-02-19 fix misalignments, turn center post into hole for separate post
    [battery_box.scad, battery_box.stl]
2023-02-19 remove power boost tray, tweak dimensions
    [board_tray2.scad, board_tray2.stl]
2023-02-19 make power boost holder separate
    [power_boost.scad, power_boost.stl]
